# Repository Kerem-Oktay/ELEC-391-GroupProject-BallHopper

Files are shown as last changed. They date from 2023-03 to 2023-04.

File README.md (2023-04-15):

# Ball Hopper: Gripper Robot
ELEC 391 - Electrical Engineering Design Studio II (January - March 2023)

### Team Members
- Analog Electronics: [Idil Bil](https://github.com/idil-bil)
- Digital Electronics: [Kerem Oktay](https://github.com/Kerem-Oktay)
- Optimal Control: [Phi Lam](https://github.com/philam2001)
- System Identification: [Jaydon Alexis](https://github.com/jaydonalexis)

## Proof of Concept Videos
### Analog 
- Homing Circuit: https://drive.google.com/file/d/1XPwnbltA7bYrDxhqjHbavb2MQuFamWF6/view?usp=sharing
- Motor Driver Response to PWM Signals: https://drive.google.com/file/d/1h0WLaYGfkV7tp02XX7nt_eYF0rJrJksn/view?usp=sharing

### Digital
- Missed Pulses Test: https://drive.google.com/file/d/1QNyGvOfNERpase1NgM-POGZV6O9L-rX4/view?usp=sharing
- Both Directions Counting: https://drive.google.com/file/d/1wTb4RRv8bWMMX-Ec8G-Ff5oxxHRGX3V3/view?usp=sharing

### Optimal Control
- Gripper Mechanism Control: https://drive.google.com/file/d/1wUlJKEUdJ5kxWtdi2DNFExJYAqgorsBL/view?usp=sharing
- Interrup Service Routine Running: https://drive.google.com/file/d/1-M_vfCSoojId2iBqmILGAV9uz4eYeyNS/view?usp=sharing

### System Identification
- Gripper Mechanism Simulation on MATLAB/Simulink: https://drive.google.com/drive/folders/1JD9nbEjx4Q1AWdH3Mn-C0eqIqGHE8A6V?usp=sharing

## Other Videos
- The control system working before integration, with sensors: https://drive.google.com/file/d/1pgXOPBrIMusSZi8hItNfwTtvf7tGX0xt/view?usp=sharing
- Motor moving the fingers: https://drive.google.com/file/d/19ZQQKfPF29rKkGoej6QkP3fz3SBA11u9/view?usp=sharing
- The finger picking up a tennis ball: https://drive.google.com/file/d/1Nz7Qj5wmDarD6SwZJ-01VuMlN-VZ1lDX/view?usp=sharing

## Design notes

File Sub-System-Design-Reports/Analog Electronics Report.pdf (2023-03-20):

1

### Ball Hopper – Analog Electronics

White Paper | Updated – March 19, 2023
Idil Bil, Group Portugal, ECE, University of BC, Vancouver, BC, Canada

Abstract
An electrical hardware system for an autonomous tennis ball gripping robot is designed. The system consists of a microcontroller (ESP32), various peripherals, proximity sensors and a motor driver. Peripherals are used to interface with the user, proximity sensors are used to detect the objects and the destination, while the motor driver is used to control the motor.

In this paper, Section 1 defines the Analog sub-system behavior and identifies the RCGs to achieve that. Section 2 explains the design process for the sub-system including Part Selection, Motor Driver Design and PCB Design using MATLAB and Altium CircuitMaker. Lastly, Section 3 talks about the tests executed to verify if the designs satisfy the RCGs.

Nomenclature
RCG Requirement, Constraint, Goal PCB Printer Circuit Board
cm centimeter
A ampere
V voltage
ms | millisecond
IC | Integrated Circuit
MCU Microcontroller
PJA Power Jack
I/O Input/output
PLD Programmable Logic Device DC Direct Current
OTS Off the Shelf

2

MHz Mega Hertz
CPU Central Processing Unit
UART Universal Asynchronous Receiver/Transmitter SPI Serial Peripheral Interface
CPR Counts per Rotation
DRC Design Rule Checker
PWM Pulse Width Modulation LED Light Emitting Diode

### 1. RCG Identification

This project is an autonomous gripper robot. To ensure autonomous functionalities an analog electronic subsystem is designed. The system must have certain peripherals, proximity sensors, a motor to detect and grasp objects. In addition, a microcontroller is needed to use the mentioned devices. For this functionality the following 5 RCGs for the related issues are identified as shown in Figure 1.

Issue | Requirement | Constraint | Goal
Motherboard PCB | Board must fit a 6x8 cm area | All the peripherals need to align with proper mechanical placement in the enclosure box | Minimize board size
Motor Driver PCB | Board must fit a 6x5 cm area | Traces for the motor must hold up to 5 A | Minimize board size
Motor Driver Power Consumption | Must not consume more than 0.3 A at 12 V under no-load conditions | Power consumption can’t be smaller than 0.15 A at 12 V | Minimize the power consumption
Motor Driver Response | Step response settle time must be smaller than 200 ms | A minimum of 15% duty cycle is needed for the PWM to generate the response | Minimize the settle time

3

Homing
Circuit

Must be suited
for mechanical
interaction
between the
circuit and
fingers

Can’t be too sensitive, so it doesn’t register false homing

Minimize the
response
time

Figure 1: Analog Electronic RCG’s

### 2. Sub-System Design

In this section, the design choices for the hardware are explained. As a start, the High-Level Hardware Design talks about the overall architecture. Then, Part Selection specifies the electronic components chosen and why. Motor Driver Design explains the chosen IC and the characterization process. After that, Motherboard and the Motor Driver PCB Design explains the respected PCB design processes.

### 2.1 High-Level Hardware Design

Figure 2 presents the high-level architecture of the hardware. The functionalities of the blocks are as follows.

Power
- PJA: Supplies 12 V to the electronics.
- Power Regulator: Converts the 12 V input from the power jack into regulated 5V for other devices.
I/O
- Debug Port: Used to interface with the microcontroller.
- Digital Phone Jack: Used to reset and communicate the state of the gripper. Sensors
- Ultrasonic Sensor: Measure the distance between the gripper and the floor to detect when to grab objects.
- Hall Sensor: Detects the destination marker for object collection.

4

Motor Driver - Homing Circuit: Used to identify the end points of the fingers to start the reset

procedure. - Motor: Is the DC motor chosen in the System Identification Report. - Control Circuit: Is the Motor Driver Circuit explained in Section 2.3. - Decoder: Counts the pulses coming from the build-in encoder of the motor. - PLD: Acts as a multiplexer to feed the count bits to the microcontroller.

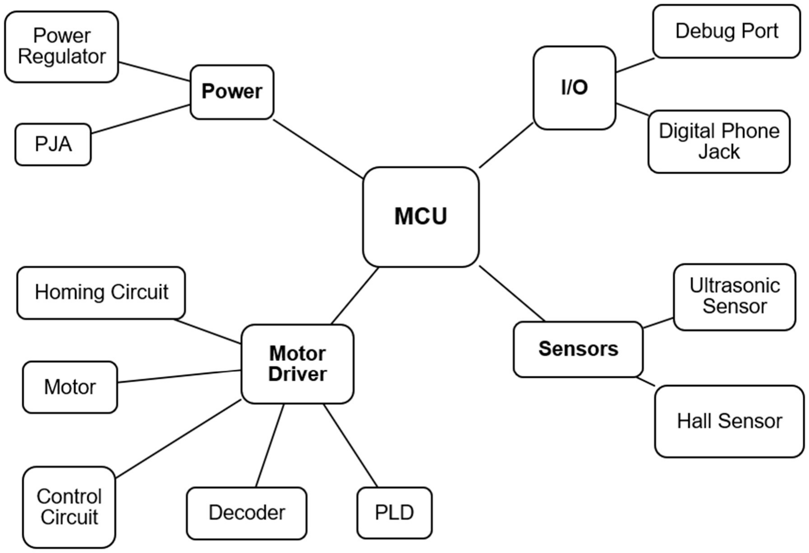
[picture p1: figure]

Figure 2: High Level Architecture Diagram

### 2.2 Part Selection

In order to achieve the functionalities mentioned above the following OTS products are selected and their connections are shown in the schematic prepared with Altium CircuitMaker in Figure 3:

5

ESP32-DOIT-DEVKIT V1 [1] is chosen as the microcontroller as it has the chip ESP32-D0WDQ6 [2], which provides 4 timers, 19 general purpose I/O and a prebuild debug port. It has a clock frequency between 80 MHz and 240 MHz, this is believed to be enough for our software in our current stage. It also provides dual CPU cores, that can be used for running multiple software simultaneously and supports a high variety of interfaces such as UART, SPI and Ethernet, which can be used for integration.

PJA is a user defined interface, so the device PJ-102A [3] given to us was used. For voltage regulation LM7805CT [4] is used as it provides regulated 5 V given a 12 V input.

Digital Phone Jack is also a user defined interface, so the device SJ1-3544N [5] given to us was used. Debug port is present in the chosen microcontroller.

The Ultrasonic Sensor is chosen as HC-SR04 [6] as it is a widely used and accurate ultrasonic sensor in the market. For the Hall Sensor the SS411P [7] is chosen because it has a build-in pull up resistor making the integration with the microcontroller simpler.

SS-01GLP [8] limit switch is used for the homing circuit as it provides mechanical interface that can be triggers using the fingers of the claw. The motor chosen is from Pololu with the item number 2821 [9]. This motor coming with a build-in encoder, has 64 CPR and needs a 12 V input, which fits our power circuit. Further explanation is in the System Identification Report. The decoder HCTL-2022 [10] is chosen because of reasons explained in the Digital Electronics Report. The Atmel ATF16V88 [11] PLDs are used as 4-1 multiplexers, which is also explained in the Digital Electronics Report. Lastly, the Control Circuit is a Motor Driver IC explained in Section 2.3.

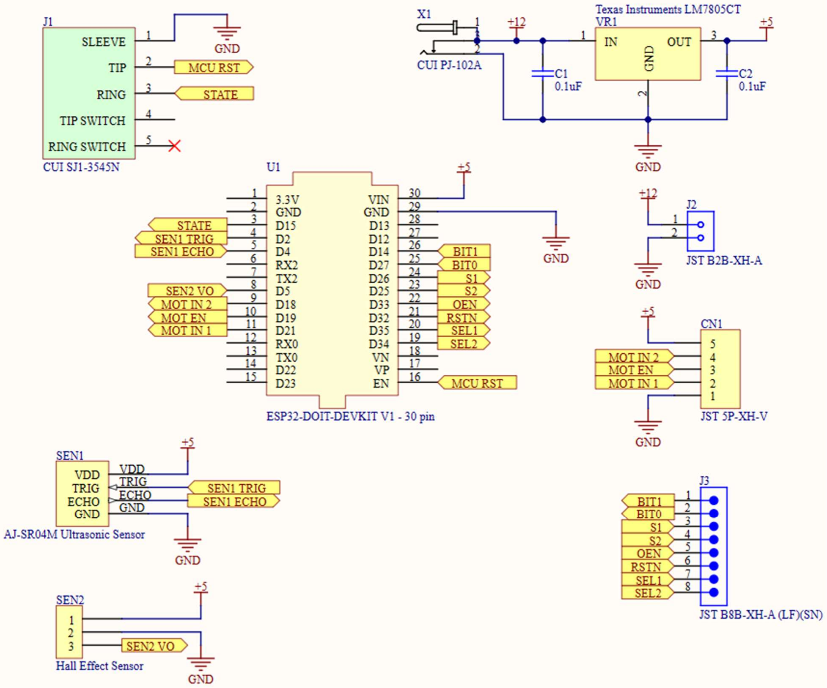
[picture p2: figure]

6

Figure 3: Motherboard Schematics

### 2.3 Motor Driver Circuit Design

The chosen motor driver being used is L298 Dual Full-Bridge Driver [12]. It’s block diagram obtained from the datasheet is shown on Figure 4. On the diagram, pin VS and VSS are respectively supply voltage and logic supply voltage. Pin numbered 8 is ground, pins labelled In1 and In2 are input signals for one H-bridge. Pin labelled EnA is the enable pin for the H-bridge of one motor. Out1 and Out2 are the output pins of that H-bridge and they connect to the motor chosen. Rest of the pins are not used as they are for a second motor which is not used in this project.

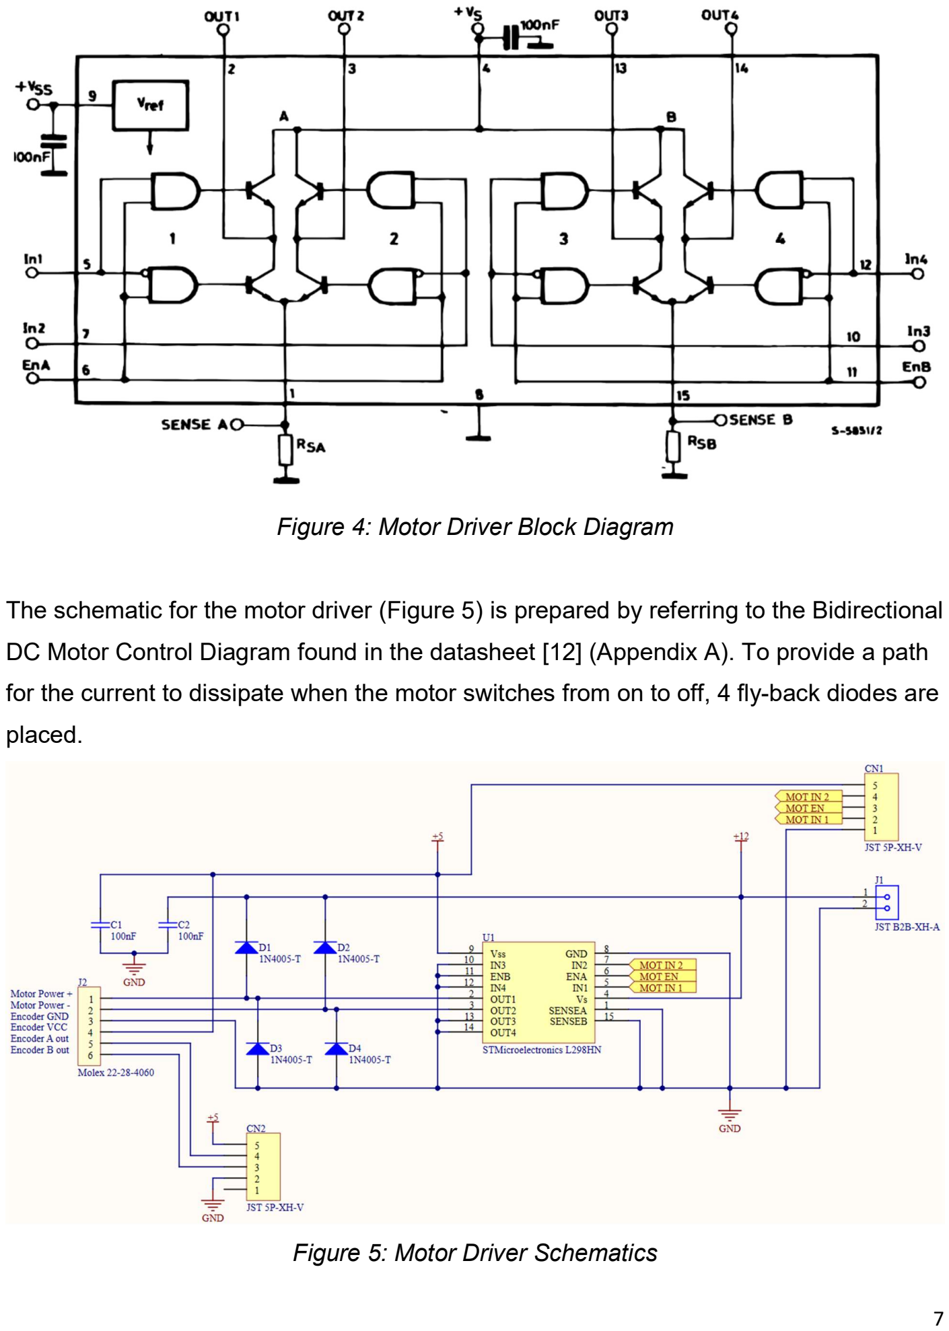
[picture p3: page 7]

7

Figure 4: Motor Driver Block Diagram

The schematic for the motor driver (Figure 5) is prepared by referring to the Bidirectional DC Motor Control Diagram found in the datasheet [12] (Appendix A). To provide a path for the current to dissipate when the motor switches from on to off, 4 fly-back diodes are placed.

Figure 5: Motor Driver Schematics

8

The characterization of the motor is done by collecting data from the oscilloscope to be used by Optimal Control. 5 V was given to In1 and In2 of the motor driver to get the step response seen in Figure 6.

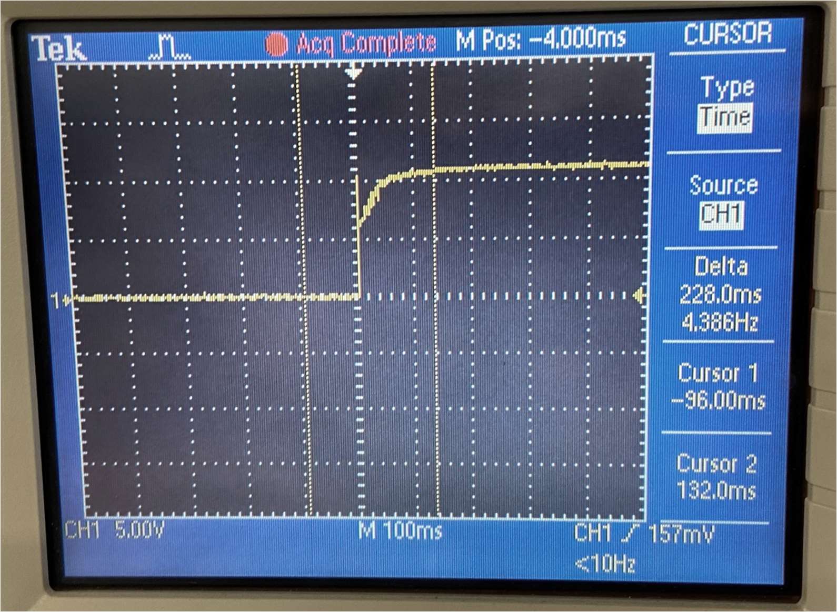
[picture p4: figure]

Figure 6: Step Response of the Motor Driver

This data acquisition is done multiple times to calculate the approximate settle time as 130 ms and the MATLAB code found in Appendix B is used to calculate the transfer function in Figure 7 and the step response in Figure 8. The settle time was lower than 200 ms and it was only consuming around 0.21 A at 12 V. Since these satisfies the RCGs and the step responses looked similar this driver was chosen.

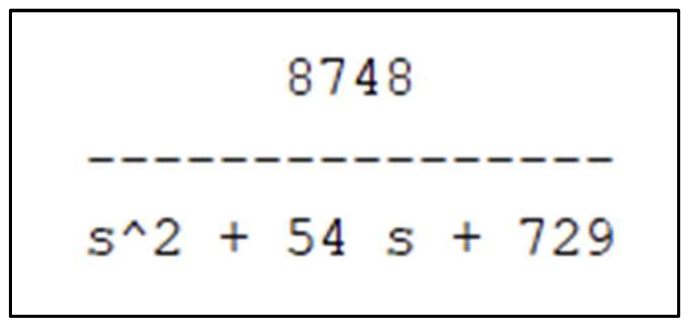
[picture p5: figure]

Figure 7: Motor Driver Transfer Function

9

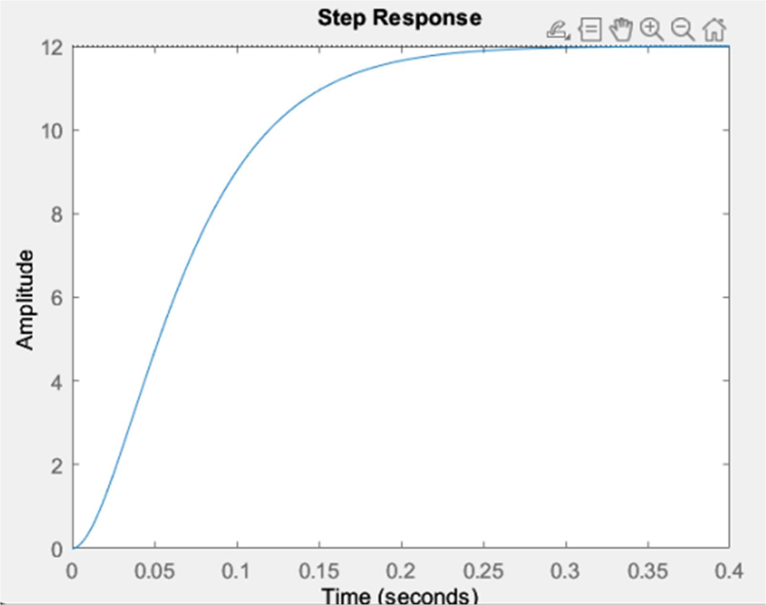
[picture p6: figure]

Figure 8: Motor Driver Step Response

### 2.4 Motherboard and Motor Driver PCB Design

Using Altium CircuitMaker, a Motherboard for the Microcontroller and the peripherals, as well as, a Daughterboard for the Motor Driver Circuit are designed. The boards are 2-layered with no ground plane. Each board has dedicated XH-connecters for board-toboard connections. All the components are properly named, and their labels can be seen on the silkscreens. Figure 9 and 11 show the PCB schematics, while Figure 10 and 12 show the 3D view of the PCBs.

To meet the size RCG, the PLDs and the decoder were put on a different Daughterboard that is explained in the Digital Electronics Report.

10

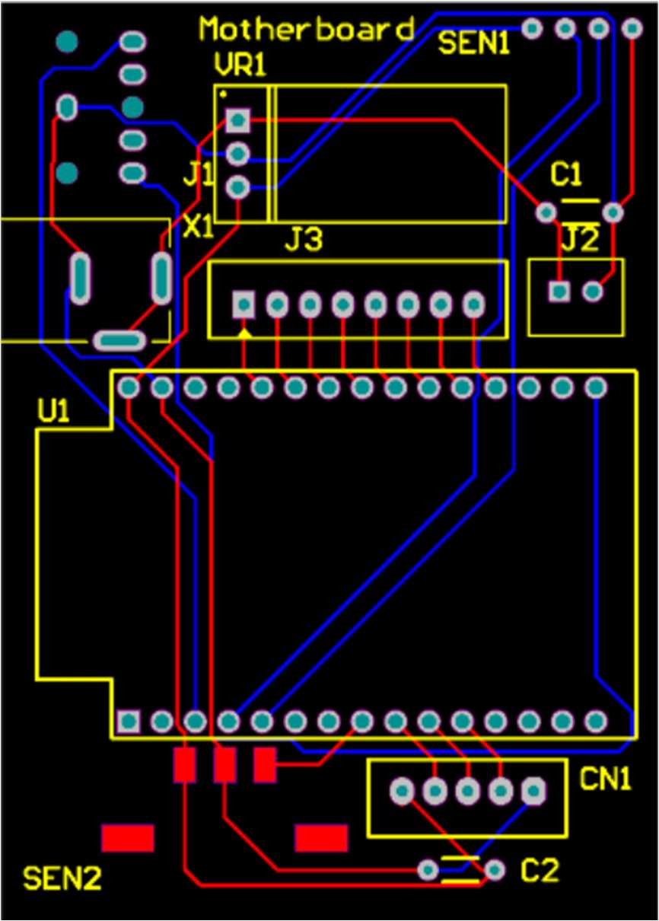
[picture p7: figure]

Figure 9: 2D View of the Motherboard PCB

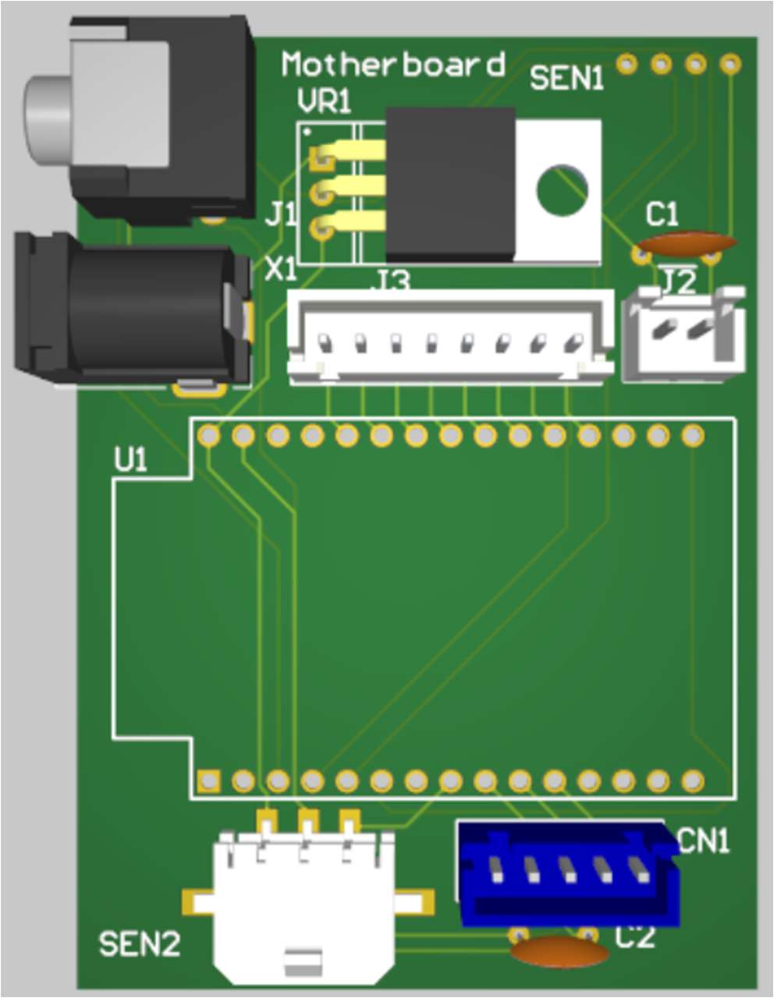
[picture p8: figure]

Figure 10: 3D View of the Motherboard PCB

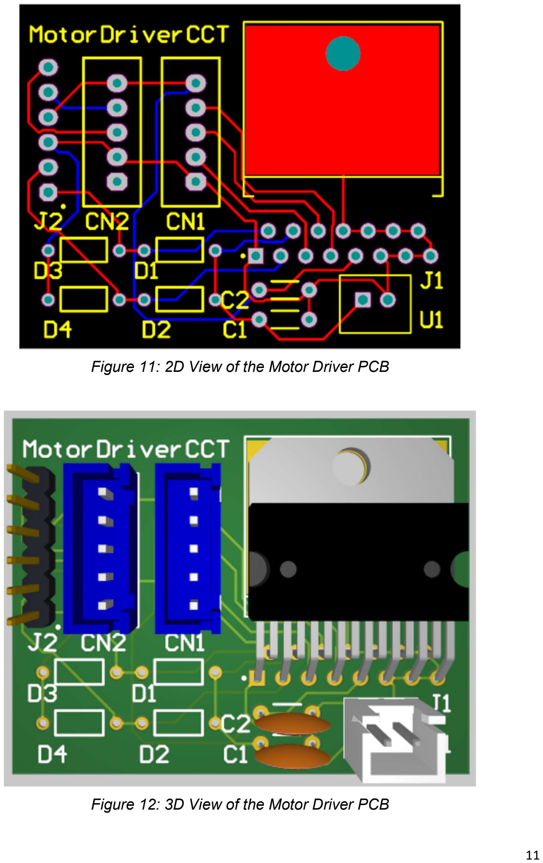
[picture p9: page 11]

11

Figure 11: 2D View of the Motor Driver PCB

Figure 12: 3D View of the Motor Driver PCB

12

### 3. Testing of the Design

The 5 RCGs listed in Section 1 are either individually tested or considered in the design process. The tests executed, and their results are explained below.

### 3.1 Motherboard PCB

The “Run DRC” feature in Altium CircuitMaker is used to verify the PCB design made, refer to Appendix C for the “DRC Report”. The size requirement was kept in mind while designing the board for the first iteration. Iterations following that focused on minimizing the board size. Current board size is 5x7 cm, the RCG has been met.

### 3.2 Motor Driver PCB

Same approach as the Motherboard is used when designing the PCB for the Motor Driver. The “Run DRC” feature in Altium CircuitMaker is used to verify the PCB design made, refer to Appendix D for the “DRC Report”. First iteration was made while keeping the size requirement in mind and the following iterations minimized the board size. Current board size is 4.5x3.5 cm, the RCG has been met.

### 3.3 Motor Driver Power Consumption

Multiple tests where the Motor Driver was connected to a 5 V input were run. Figure 13 shows the power supply photo where the current was as low as 0.18 A. However, on average the power consumption under a no-load case was found to be 0.21 A at 12 V. These numbers meet the RCGs identified.

13

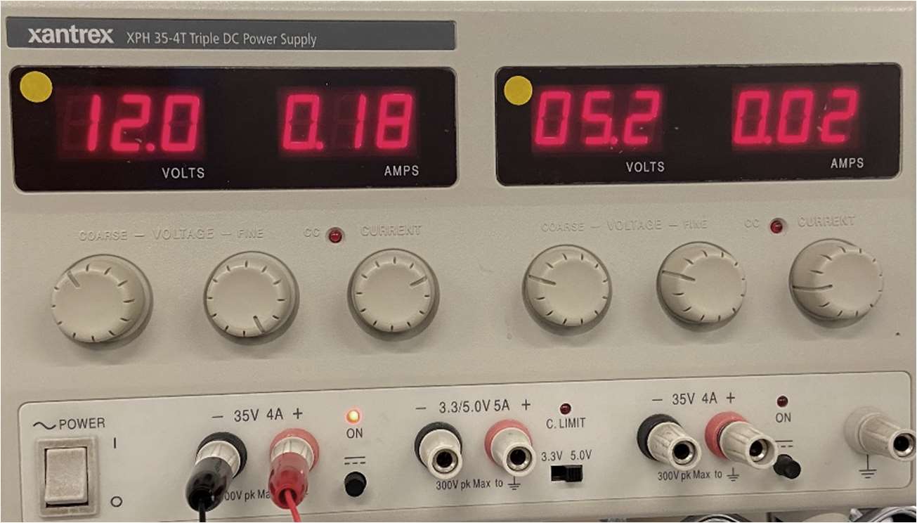
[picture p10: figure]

Figure 13: Power Supply Data for the Motor Driver

### 3.4 Motor Driver Response

As seen in Section 2.3 the Motor Driver has a settle time of 130 ms. Other tests were run with a custom build H-bridge, which also consumed 0.2 A at 12 V under no-load conditions. However, it had a settle time of 180 ms, so due to the lower settle time of the IC, L298 was chosen as the Motor Driver. Refer to Appendix E for the step response of the H-bridge.

The video “Motor-Driver-Response-to-PWM Signals” (https://drive.google.com/file/d/1h0WLaYGfkV7tp02XX7nt_eYF0rJrJksn/view?usp=shari ng) shows the Motor Driver operating under different PWM duty cycles. When the duty cycle is doubled the speed also approximately doubled. This data can be seen on the proof of concept video.

### 3.5 Homing Circuit

A straightforward test circuit was prepared for the limit switch. By clicking the switch, the circuit was complete, and the LED was lit. Since this mechanical interface can be used with the fingers of the gripper, this component can be used as the Homing Circuit and

14

the RCG is met. Refer to the video “Homing-Circuit” (https://drive.google.com/file/d/1XPwnbltA7bYrDxhqjHbavb2MQuFamWF6/view?usp=sh aring) to see the test being run.

References
[1] “ESP32-DevKitC V4 Getting Started Guide - ESP32 - — ESP-IDF Programming Guide latest documentation,” Espressif.com, 2016. [Online]. Retrieved March 19, 2023, from https://docs.espressif.com/projects/esp-idf/en/latest/esp32/hw-reference/esp32/get-starteddevkitc.html.
[2] ESP32 Series Datasheet Including. (n.d.). Retrieved March 19, 2023, from https://www.mouser.ca/datasheet/2/891/Espressif_Systems_01292021_esp32-1991551.pdf
[3] "PJ-102A Datasheet - Jacks | Dc Power Connectors | CUI Devices," Retrieved March 19,
2023, from https://www.mouser.ca/datasheet/2/670/pj_102a-1778834.pdf
[4] "LM78XX, LM78XXA - 3-Terminal 1 A Positive Voltage Regulator," . Retrieved March 19, 2023, from https://www.mouser.ca/datasheet/2/308/LM7805-1301244.pdf
[5] "SJ1-354XN Series Datasheet - Jacks | Audio Connectors | CUI Devices," . Retrieved March
19, 2023, from https://www.mouser.ca/datasheet/2/670/sj1_354xn_series-1779189.pdf
[6] "HC-SR04," . Retrieved March 19, 2023, from https://www.electroschematics.com/wpcontent/uploads/2013/07/HCSR04-datasheet-version-1.pdf
[7] "SS311PT/SS411P Bipolar Hall-Effect Digital Position Sensor ICs with Built-in Pull-up Resistor," . Retrieved March 19, 2023, from https://prodedam.honeywell.com/content/dam/honeywell-edam/sps/siot/en-us/products/sensors/magneticsensors/bipolar-position-sensor-ics/common/documents/sps-siot-ss311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
[8] “SS-P," . Retrieved March 19, 2023, from https://omronfs.omron.com/en_US/ecb/products/pdf/en-ss_p.pdf

15

[9] "MOT2-info.pdf," . Retrieved March 19, 2023, from https://people.ece.ubc.ca/~engservices/files/courses/elec391-data_sheets/MOT2-info.pdf
[10] "HCTL-2032,2022.pdf," . Retrieved March 19, 2023, from https://media.digikey.com/pdf/Data%20Sheets/Avago%20PDFs/HCTL-2032,2022.pdf
[11] "ATMEL ATF16V8B" . Retrieved March 19, 2023, from http://ww1.microchip.com/downloads/en/devicedoc/atmel-0364-pld-atf16v8b-8bq-8bqldatasheet.pdf
[12] "Dual full-bridge driver," . Retrieved March 19, 2023, from https://www.sparkfun.com/datasheets/Robotics/L298_H_Bridge.pdf

Appendix
A: Bidirectional DC Motor Control Block Diagram

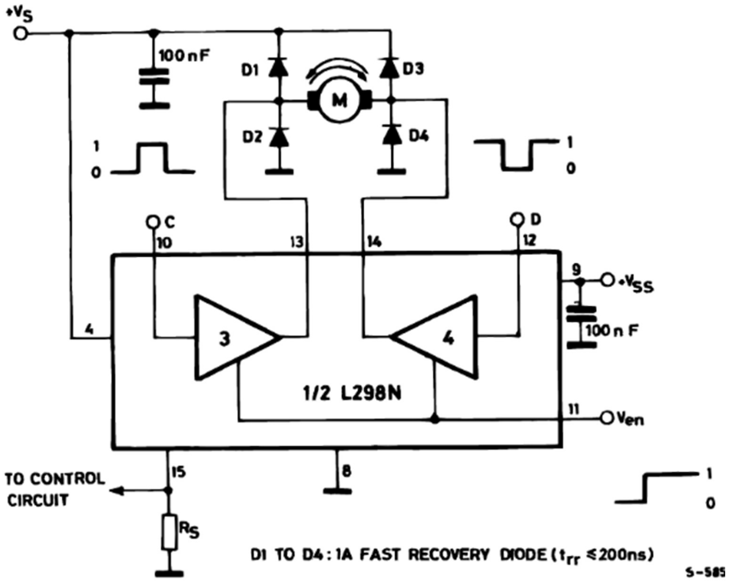
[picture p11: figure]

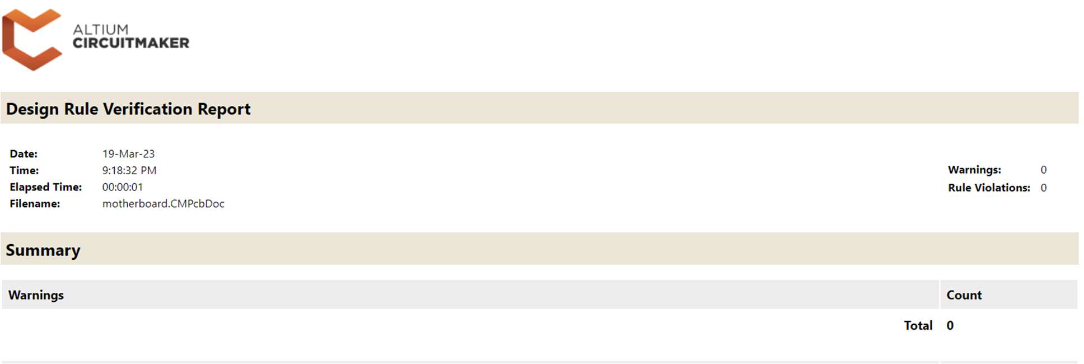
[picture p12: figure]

16

B: MATLAB Code for the Transfer Function

function naturalFrequency = getSettleTimeNaturalFrequency(settleTime, dampingCoefficient, timeConstantMultiplier)

naturalFrequency = fraction(timeConstantMultiplier, (dampingCoefficient * settleTime));

end

timeConstantMultiplier = 5

dampingCoefficient = 1

function transferFunction = getTransferFunction(naturalFrequency, gain, dampingCoefficient)

transferFunction = minreal(tf((((naturalFrequency)^2) * gain), [1 (2 * dampingCoefficient * naturalFrequency) ((naturalFrequency)^2)]));

end

C: DRC Report for the Motherboard

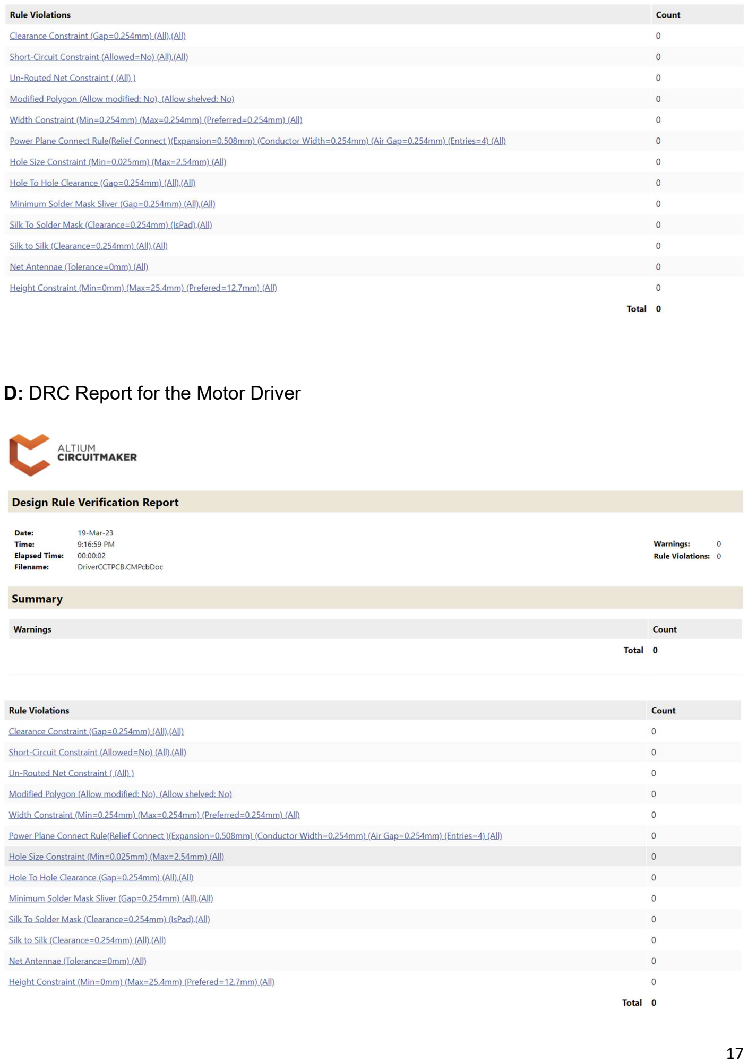
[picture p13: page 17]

17

D: DRC Report for the Motor Driver

18

E: Step Response of the Custom Build H-Bridge

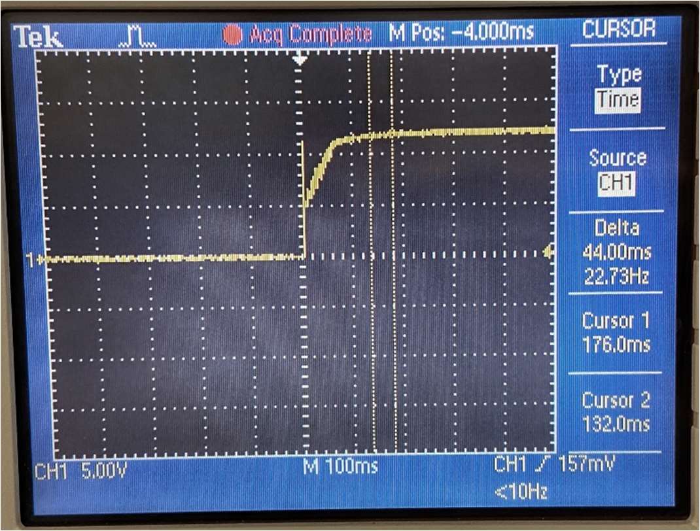
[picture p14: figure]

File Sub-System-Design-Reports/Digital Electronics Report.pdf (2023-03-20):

1

Ball Hopper – Digital Electronics

White Paper | Updated – March 19, 2023
Kerem Oktay, Group Portugal, ECE, University of BC, Vancouver, BC, Canada

Abstract
A pulse counter-decoder system counting the encoder A and B signals coming from a built-in encoder of a motor is designed. The system consists of a quadrature decoder, HCTL-2022, and two PLDs, Atmel ATF16V8B, that are programmed as 4 to 1 multiplexers. Decoder reads the raw encoder signals coming from the motor and converts them to a single 32-bit count value. Multiplexers are used to minimize wiring while keeping maximum bits for the count signal. C code is developed to read the signal and convert it to motor angle value for later usage.

In this paper, Section 1 defines the sub-system behavior and identifies the RCGs to achieve the behavior. Section 2 explains the Sub-System design by going through the parts of the system and the design process using tools such as WinCUPL/WinSim and Altium CircuitMaker. Finally, Section 3 goes over the tests executed to verify the designed system satisfies the RCGs. Nomenclature
RCG | Requirement, Constraint, Goal
IC | Integrated Circuit
MHz | Mega Hertz
CW/CCW Clockwise/Counter-Clockwise
MCU | Microcontroller Unit
CPR | Counts Per Revolution
PCB | Printed Circuit Board
DRC | Design Rule Check
MUX | Multiplexer
PLD | Programmable Logic Device
PWM | Pulse Width Modulation
POC-VID Proof of Concept Video

2

### 1. RCG Identification

In this project a DC motor with a built-in encoder is used. A digital electronics sub-system is designed to ensure proper reading and converting of the pulses coming from the encoder. The system must read the encoder A and B signals, count the pulses while keeping track of the direction and convert the count value into motor angle. From this defined functionality of the system, the following 5 RCGs for related issues are identified as shown in Table 1.
Issue | Requirement | Constraint | Goal
Pulse Counting | The system must not miss more than 10 pulses per 100 pulses. | The clock frequency of the decoder IC cannot exceed 33MHz. | Minimize the number of missed pulses.
Motor Direction Detection | The system must realize when the motor is rotating in CW and CCW directions. | Negative directions must be registered as 2’s complement values. | Minimize the usage of different logic for the direction detection.
Wiring/Bit Usage | Pulses must be counted with at least 10 bits to avoid quick overflows. | Atmel ATF16V8Bs (PLDS) have a set number of Input and Output pins. | Maximize the bits for counting and minimize external wiring of the MCU.
Pulse Conversion into Degrees | Angle value resolution must be at least the same as the resolution CPR of the encoder. | The encoder has a set value of 64 CPR. | Maximize the resolution of the degree values.
Daughter Board | The PCB must be smaller than 6x6 cm. | The PCB cannot violate any DRC points. | Minimize the size of the PCB.

Table 1: Digital Electronics Sub-System RCGs

3

### 2. Sub-System Design

This sub-system consists of HCTL-2022, a Quadrature Decoder / Counter Interface IC, and 2 PLDs. This section first goes over the characteristics of the quadrature decoder IC. Afterwards, it explains the high level and 4-1 MUX design. Finally, it presents the integration of HCTL-2022 and 4-1 MUXs, the PCB design and the C code developed for degree value conversion.

### 2.1. HCTL-2022 Characteristics

HCTL-2022 counts the pulses of an encoder given the A and B signals as input. It counts with 32 bits and can run up to 33 MHz clock frequency. It has tri-state buffers to output a single byte (8 bits) of the count value. The pinout of the IC is shown at Figure 1. This diagram is obtained from the datasheet of the IC [1]. Pins D0-D7 are the 8 bits of a selected byte. Pins SEL1 and SEL2 are selection signals for outputting certain bytes of the count value. OE pin is used to enable/disable the tri-state buffers and RST pin is used to reset the IC. CHA and CHB are the input signals fed from the encoder of the motor. Other pins are not used in this design.

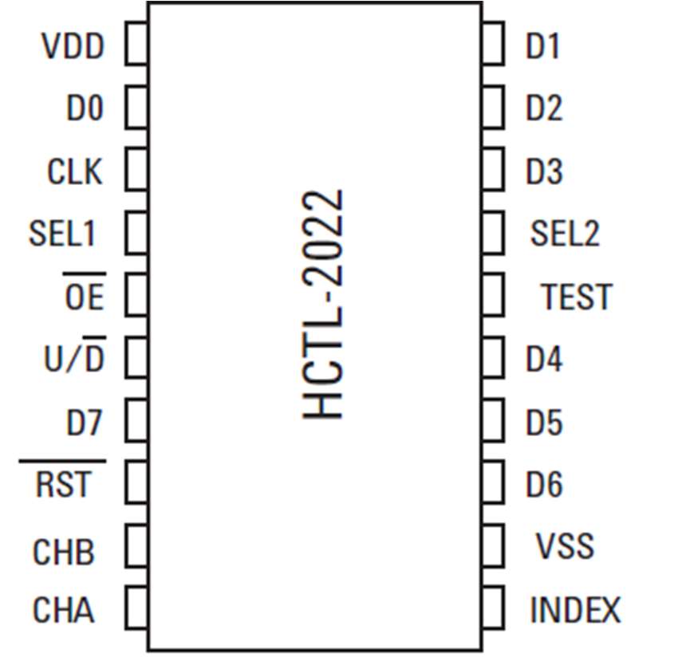
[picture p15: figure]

Figure 1: Pinout of HCTL-2022 Due to the digital noise filtering, high clock frequency, 32 bits up and down counting and latch capabilities; HCTL-2022 is chosen in this design. These features address the Pulse Counting, Motor Direction Detection and Wiring/Bit Usage RCGs.

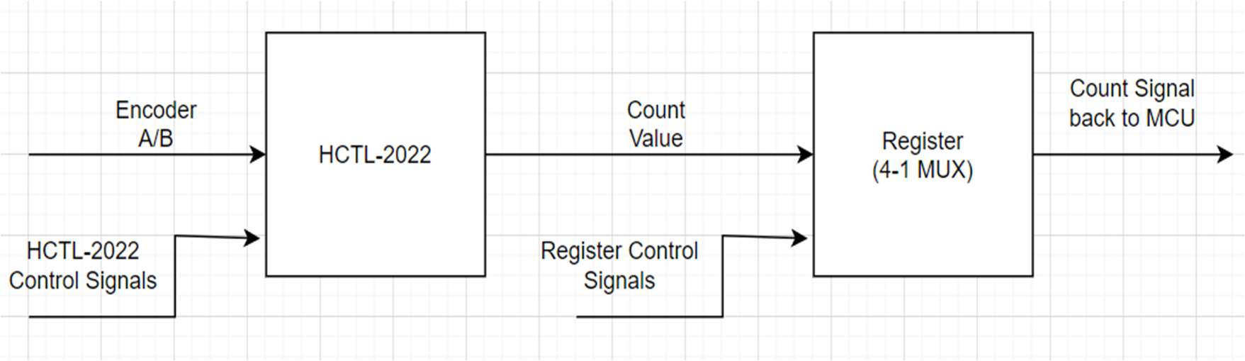
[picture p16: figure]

4

### 2.2. High Level Decoder Design

The high-level decoder system design is shown at Figure 2. The system is provided encoder A and B signals, and control signals for HCTL-2022 and register block. The chosen register block is a 4-1 MUX. The count value is fed back to an MCU.

Figure 2: High-Level Decoder System Design Since HCTL-2022 needs 8 bits for its output and 4 bits for its control, using it alone requires 12 bits that needs to be externally wired to MCU board. By using two 4-1 MUXs, there are only 2 bits for output and 2 bits for MUX control in addition to the 4 bits for HCTL-2022 control. This adds to 8 bits which satisfies the goal of “Wiring/Bit Usage” RCG. This way a single byte is read in 4 pairs of bits.

2.3. 4-1 MUX Design
Atmel ATF16V8B model PLDs are used to design the 4-1 MUXs. The truth table for a 4-1 MUX is shown at Table 2. S1 and S2 are selection signals. Q0 is the output of the MUX and D0-D3 are the input signals.
S1 | S2 | Q0
0 | 0 | D0
1 | 0 | D1
0 | 1 | D2
1 | 1 | D3
Table 2: 4-1 MUX Truth Table

5

By observing the truth table, the following circuit schematics in Figure 3 is built using logic gates. S1 and S2 are the same signals as on the Truth Table, I0-I3 correspond to D0-D3 and Y corresponds to Q0.

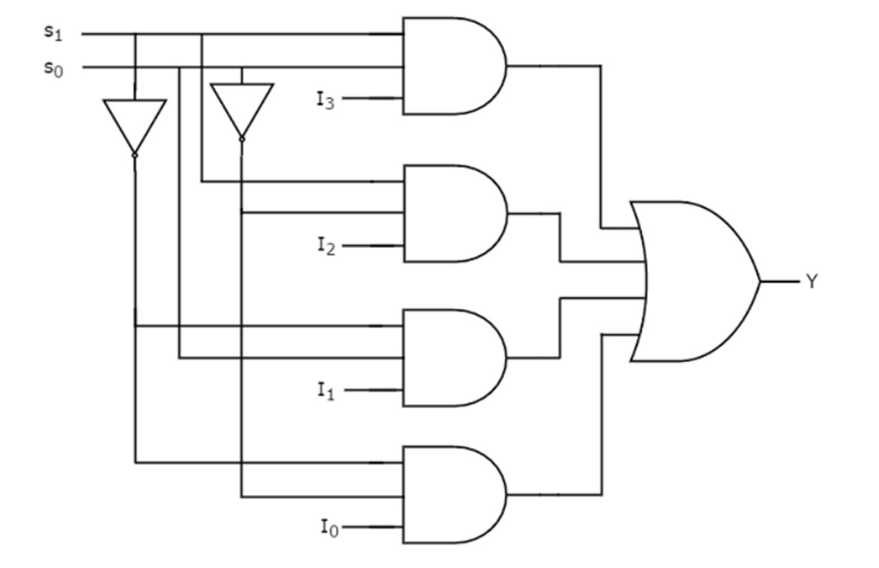
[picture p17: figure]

Figure 3: 4-1 MUX Circuit Schematic with Logic Gates [2] The logic equation written in CUPL language in WinCUPL is as follows (1). The variables are the same signals as shown on the Truth Table.

Q0 = (D0 & !S1 & !S2) # (D1 & S1 & !S2) # (D2 & !S1 & S2) # (D3 & S1 & S2); (1)

The design is simulated using WinSim and the following waveform is obtained shown at Figure 4. The waveform matches with the desired Truth Table.

6

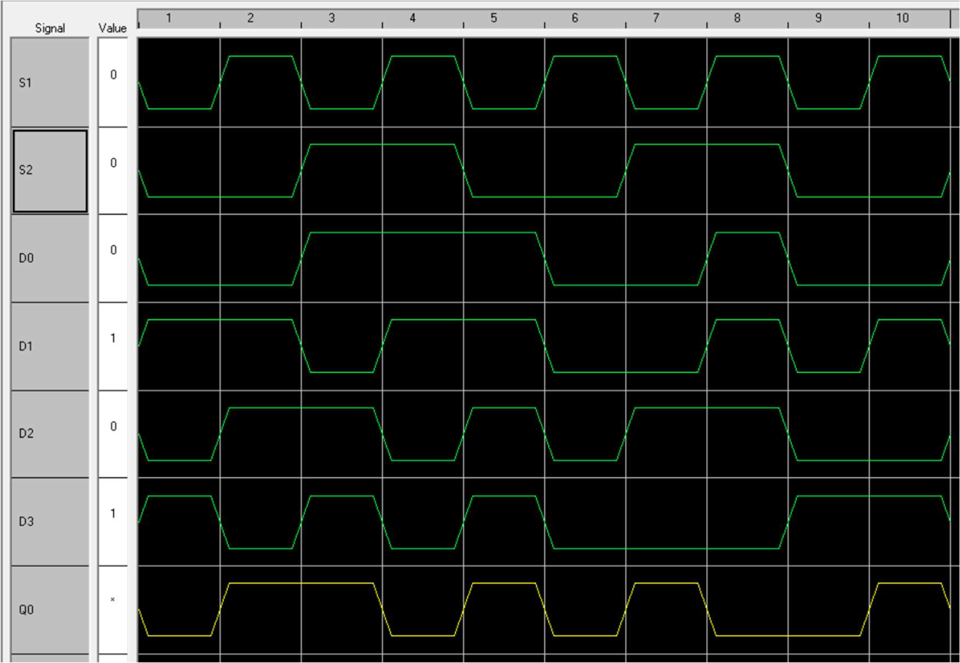
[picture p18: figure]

Figure 4: 4-1 MUX Simulated Waveform

### 2.4. HCTL-2022 IC and 4-1 MUX Integration

HCTL-2022 and 4-1 MUXs (PLDs) are integrated by simply connecting the D0-D3 outputs of the HCTL-2022 to inputs of one of the MUXs and D4-D7 outputs to the inputs of the other MUX. All control signals are fed from an MCU and output signals BIT0 and BIT1 are fed back to the MCU. The schematic prepared with Altium CircuitMaker is shown in Figure 5. Connectors are added for wiring between the motherboard and a crystal is added to provide clock for HCTL-2022.

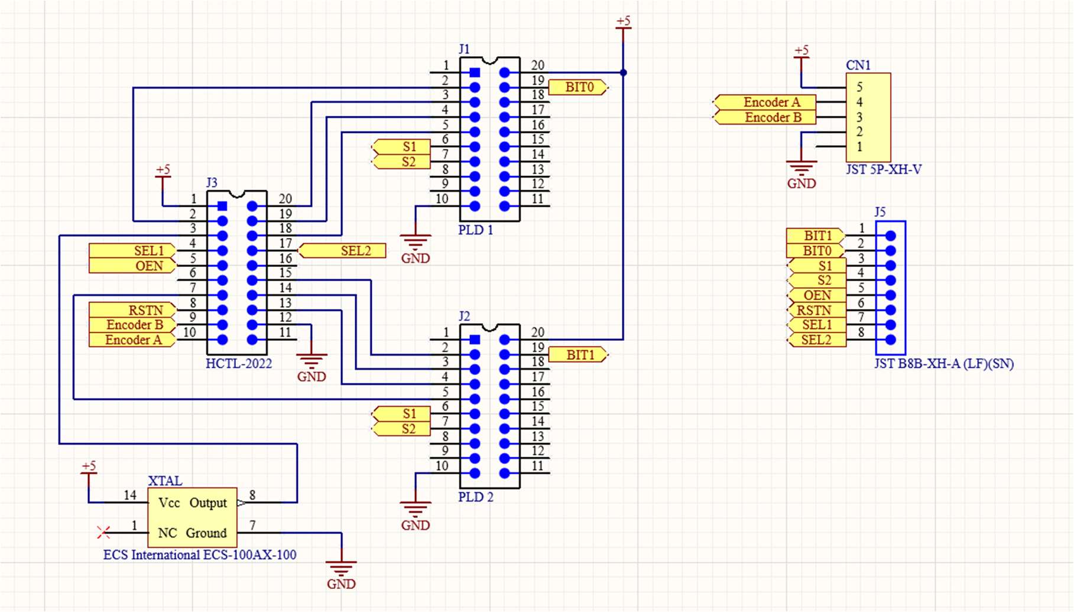
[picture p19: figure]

7

Figure 5: Decoder System Circuit Schematic

### 2.5. Daughter Board PCB Design

Using Altium CircuitMaker a daughter board called Pulse Counter is designed. The board consists of two-layers with no ground-plane. As the HCTL-2022 and ATF16V8B devices are through hole devices, 20-pin DIP sockets are put in their places. XH type connectors are used to connect the daughter board to motor driver board and motherboard. Figures 6 and 7 show the PCB schematics and 3D view of the Pulse Counter PCB.

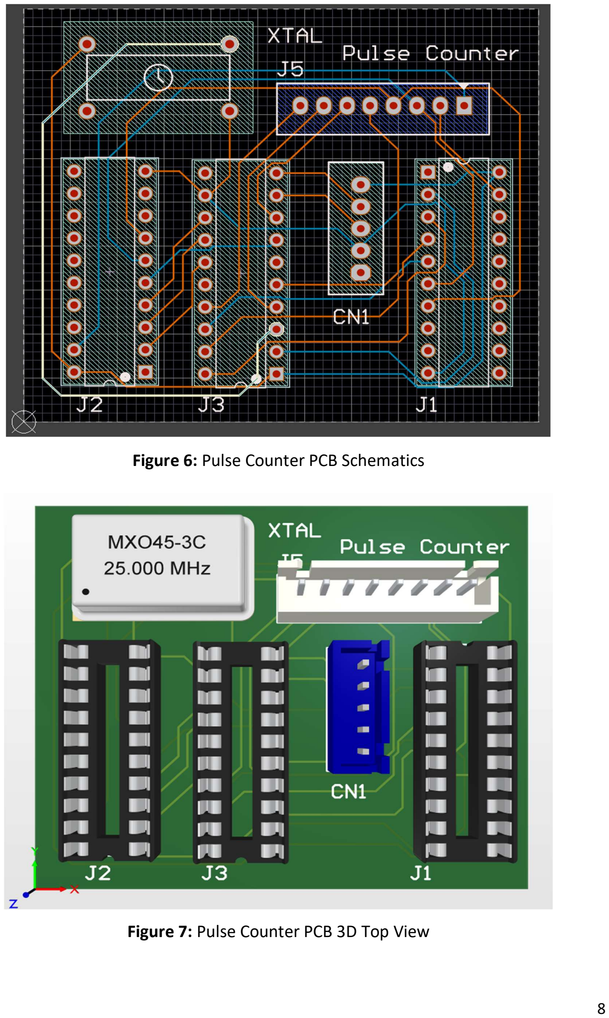
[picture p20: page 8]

8

Figure 6: Pulse Counter PCB Schematics

Figure 7: Pulse Counter PCB 3D Top View

9

### 2.6. C Code Design for Degree Conversion

As the signals coming from the decoder system are raw bits that carry the pulse count, a software routine is necessary to convert this value into degrees of the motor. In this report the C code logic is explained through an Arduino UNO board that is used for testing the system.

The routine is shown on the Flow Diagram on Figure 8. By setting SEL1 and SEL2 to corresponding HIGH and LOW values as described in page 6 of the HCTL-2022 datasheet and disabling the OE signal, certain bytes are registered [1]. Then by setting S1 and S2 signals for the 4-1 MUXs, bytes are read in 4 pairs of bits.

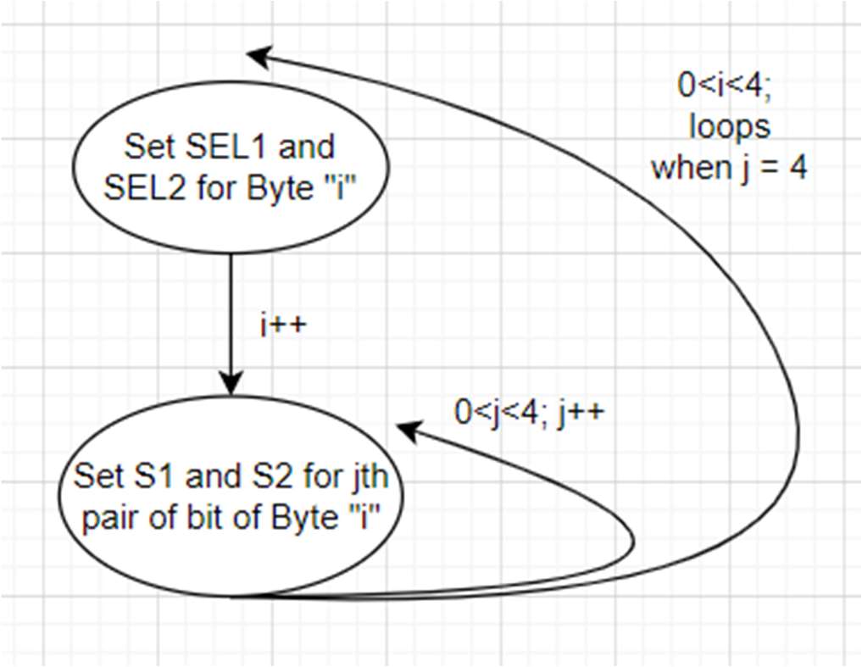
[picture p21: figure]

Figure 8: Software Routine Flow Diagram After getting all 4 bytes, these bytes are combined into a single 32 bit variable. This byte is the count value. As there is 64 CPR, it means every 360 degrees the decoder has counted 64 pulses. Therefore by multiplying the count value by 360/64, the angle value of the motor is obtained.
Please refer to the Appendix A for the full C code developed.

### 3. Testing of the Design

The 5 RCGs listed in the first section are individually tested or considered during the design process. The tests executed and their results are explained below.

10

i) Pulse Counting

After resetting the quadrature decoder and motor position, the motor driver is fed with constant 5V input. This case is assumed as the highest speed as there is no load present to slow the motor down and in terms of a PWM signal this corresponds to 100% duty cycle.

The motor is run for a certain amount of time and then stopped. The position of the motor is brought to the initial position by aligning the marker lines. The angle value (a value between 0 and 360 degrees that resets after every rotation) is seen to be 0 degrees again. This indicates no pulses were missed as any missed pulse would create an offset between the initial position and angle value of 0 degrees.

This test shows that the RCG is met. Please refer to POC-VID1 for the test being run.

ii) Motor Direction Detection

HCTL-2022 counts the pulses in both directions by increasing or decreasing the same count value. By using variable types in the C code that detect 2’s complement, negative values are detectable as well. The code does not take separate actions for two cases which means the logic is minimalized.

This shows that the RCG is met. Please refer to POC-VID2 for the test being run.

iii) Wiring/Bit Usage

HCTL-2022 counts with 32 bits which is above the 10 bits requirement. Two 4-1 MUXs in PLDs also minimize the external wire usage while keeping the same number of 32 bits counting. HCTL-2022 requires 4 wires. Using the MUXs only adds 4 more wires making a total of 8 wires.

This shows that the RCG is met during the design process.

11

iv) Pulse Conversion into Degrees

As every pulse count is registered properly by the MCU, the resolution is the same as resolution of the built-in encoder. Due to this value being set, it is also the maximum achievable resolution.

This shows that the RCG is met. Please refer to either POC-VID1 or POC-VID2 to see the angle values being reported through the serial port.

v) Daughter Board

After completing the PCB layout, “Run DRC” feature is used to verify the PCB design. While designing the board, the board size is first set to the Requirement value. After completing the design small changes are made to decrease the size of the board. The current final board is 5.5cmx4.7cm.

This shows that the RCG is met during the design process. Please refer to the Appendix B for the generated DRC document by the Altium CircuitMaker.

References

[1] "HCTL-2032,2022.pdf," . Retrieved March 19, 2023, from https://media.digikey.com/pdf/Data%20Sheets/Avago%20PDFs/HCTL-2032,2022.pdf
[2] "Digital Circuits - Multiplexers," . Retrieved March 19, 2023, from https://www.tutorialspoint.com/digital_circuits/digital_circuits_multiplexers.htm

12

Appendix A. C Code for Angle Value Conversion

// Control Signals
int RSTN = 2;
int OEN = 3;
int SEL1 = 4;
int SEL2 = 5;
int S1 = 6;
int S2 = 7;

// Counter Signals
int BIT0 = 8;
int BIT1 = 9;

volatile long count = 0;

/*
The algorithm below is based on the Example Routine given in the IC datasheet */

void setup()
{
// Assign Output Pins
pinMode(RSTN,OUTPUT);
pinMode(OEN,OUTPUT);
pinMode(SEL1,OUTPUT);
pinMode(SEL2,OUTPUT);
pinMode(S1,OUTPUT);
pinMode(S2,OUTPUT);

// Assign Input Pins

13

pinMode(BIT0,INPUT);
pinMode(BIT1,INPUT);

// Initial Decoder Reset
digitalWrite(RSTN,LOW);
delay(15);
digitalWrite(RSTN,HIGH);

// Initial Control Signals digitalWrite(OEN,LOW);
digitalWrite(SEL1,LOW);
digitalWrite(SEL2,LOW);
digitalWrite(S1,LOW);
digitalWrite(S2,LOW);

// Serial Port for Debug Purposes Serial.begin(9600);
}

byte getByte()
{
byte capture1 = 0; // Initialize a byte variable to read the first capture for(int i=0; i<4; i++){

switch(i){
case 0:
digitalWrite(S1,LOW);
digitalWrite(S2,LOW);
break;
case 1:

14

digitalWrite(S1,HIGH);
digitalWrite(S2,LOW);
break;
case 2:
digitalWrite(S1,LOW);
digitalWrite(S2,HIGH);
break;
case 3:
digitalWrite(S1,HIGH);
digitalWrite(S2,HIGH);
break;
default:
digitalWrite(S1,LOW);
digitalWrite(S2,LOW);
break;
}

capture1 |= (digitalRead(BIT0)<<i); capture1 |= (digitalRead(BIT1)<<(i+4));
}

byte capture2 = 0; // Initialize a byte variable to read the second capture for(int i=0; i<4; i++){

switch(i){
case 0:
digitalWrite(S1,LOW);
digitalWrite(S2,LOW);
break;
case 1:

15

digitalWrite(S1,HIGH);
digitalWrite(S2,LOW);
break;
case 2:
digitalWrite(S1,LOW);
digitalWrite(S2,HIGH);
break;
case 3:
digitalWrite(S1,HIGH);
digitalWrite(S2,HIGH);
break;
default:
digitalWrite(S1,LOW);
digitalWrite(S2,LOW);
break;
}

capture2 |= (digitalRead(BIT0)<<i); capture2 |= (digitalRead(BIT1)<<(i+4));
}

if (capture2 == capture1){ // If the first and second capture match then return the result byte byteCapture = capture2;
return byteCapture;
}
else getByte(); // If the first and second capture DO NOT match, try again to capture }

long combine4Bytes(byte byte4, byte byte3, byte byte2, byte byte1)
{

16

long combine = 0;
combine |= (((long)byte4 << 24) | ((long)byte3 << 16) | ((long)byte2 << 8) | ((long)byte1 << 0));
return combine;
}

void getPulseCount()
{
delay(25);
digitalWrite(OEN, HIGH); // Disable OE digitalWrite(OEN, LOW); // Enable OE

// SEL1 = 0 and SEL2 = 1 gets 4th Byte digitalWrite(SEL1, LOW);
digitalWrite(SEL2, HIGH);
byte Byte4 = getByte();

// SEL1 = 1 and SEL2 = 1 gets 3rd Byte digitalWrite(SEL1, HIGH);
digitalWrite(SEL2, HIGH);
byte Byte3 = getByte();

// SEL1 = 0 and SEL2 = 0 gets 2nd Byte digitalWrite(SEL1, LOW);
digitalWrite(SEL2, LOW);
byte Byte2 = getByte();

// SEL1 = 1 and SEL2 = 0 gets 1st Byte digitalWrite(SEL1, HIGH);
digitalWrite(SEL2, LOW);
byte Byte1 = getByte();

17

digitalWrite(OEN, HIGH); // disable OE
delay(25);
count = combine4Bytes(Byte4,Byte3,Byte2,Byte1); }

void loop() {
// put your main code here, to run repeatedly: delay(25);
digitalWrite(OEN, HIGH); // Disable OE

getPulseCount();

float angle = (count % 64)*(360.0/64.0) ; float angle_abs = (count)*(360.0/64.0) ;

Serial.print("Counter: "); Serial.println(count);

Serial.print("Angle: ");
Serial.println(angle);

Serial.print("Absolute Angle: "); Serial.println(angle_abs);

Serial.println("\n");
}

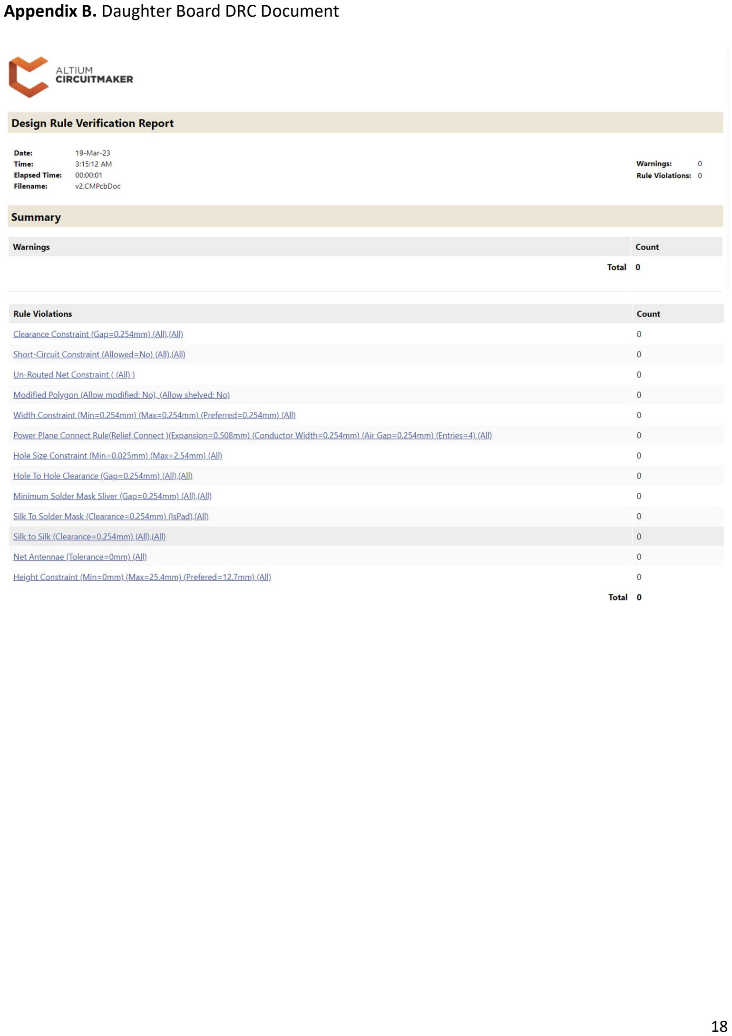
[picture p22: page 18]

18

Appendix B. Daughter Board DRC Document

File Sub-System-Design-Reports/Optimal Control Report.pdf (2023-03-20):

Ball Hopper – Optimal Control

White Paper | Updated – Mar 19, 2023
Phi Lam, Group Portugal, ECE, University of BC, Vancouver BC, Canada

Abstract
Our project is designed to be a tennis ball hopper and an important part of this robotic claw system is the control system that enables the robot to smoothly operate in different states. The claw is controlled by one PID controller model that is simulated in Simulink. The code in the MCU and the control system were designed with the idea of achieving the RCGs stated in table
1. The code compilation is done with the Arduino IDE and the selected MCU is the ESP32-Wroom-32. We created our PID with the input and output be based on the position of the
Part one of this paper indicates the five RCGs selected and maintained throughout the project term. Part two discusses the control system model and design and part three discusses the MCU and code portion to achieve our RCGs.
Nomenclature
PID | Proportional, Integral, Derivative controller
RCG | Requirement, Constraint, Goal
MCU | Microcontroller Unit

### 1. RCGs

For the optimal controls portion of this project, we require the claw to move with precision and smoothly to each of its states (origin, grasping, moving, and releasing). With this information in mind, the following RCGs are made to open and close the claw accurately without overshooting and with as minimal settling time.
RCGs | Requirement | Constraint | Goal
Settle Time | Settle time must be less than 2s | Settle time can’t be too fast that it will cause something to break | Minimize settle time as much as possible
Overshoot | Overshoot must be less than 10% | Cannot run faster than the control frequency | Minimize overshoot as much as possible

ISR | ISR frequency must be smaller than 12x the most dominant pole | Frequency cannot be faster than 10x the most dominant pole | Frequency needs to be as close to 10x the most dominant pole
State Indication | Code must exemplify what state of the design is in at a 1Hz frequency | Timer needs to have enough bits to run at 1Hz | Code needs to indicate all states as visible as possible
Rise time | Rise time must be less than 1s | Rise time can’t be faster than settling time | Minimize rise time as much as possible

Table 1: RCGs for the optimal control portion

### 2. Controller System

For our control system, we have two inputs that perform at different times, one with the goal to close the claw and one with the goal to open the claw. This feeds into our PID with K!,K", and K# parameters that is then fed into the second order amplifier. After this, we feed the signal into our electrical admittance then apply a K$ gain to it and apply a 60-ratio gain value, as the gear ratio is 60 to 1. The electrical admittance outputs a torque value which becomes the input of our mechanical admittance subsystem and outputs speed. This signal gets fed back into the admittance motor loop and a torque constant gain K%.

### 2.1 Amplifier

To enable the motor to have enough torque and power to perform its role, we use an H-bridge. We obtained our second order amplifier transfer function from using an oscilloscope to obtain data and used the MATLAB script in Appendix A to obtain the transfer function shown below (1). The step response graph of this model is also shown down in Appendix B.

(1)

### 2.2 Motor

Our electrical admittance was modelled by measuring the inductance and resistance of the motor. Through the electrical admittance model, we convert voltage to current. The represented transfer function is shown below in (2).

&

'()* = | & +.++&--.()/.&0/ (2)

### 2.3 Tuning

Combining all of these in Simulink we can get the corresponding system shown in Figure 1.

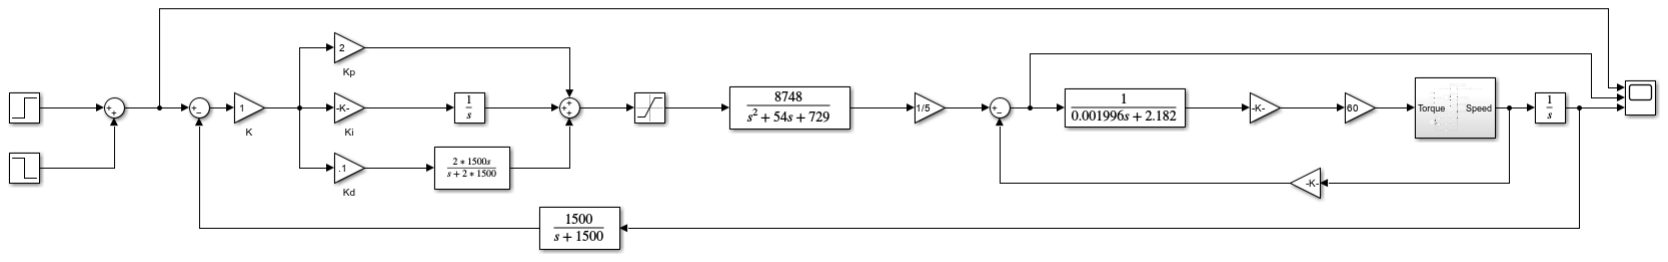
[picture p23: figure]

Figure 1: Control system of claw

Tuning the PID to the desired move in Figure 1, I use the method of manually tuning the PID following the steps noted down in my references [2]. I first set the integral and derivative gains to zero before I change the proportional gain to a small oscillating wave. Then, I increase the integral gain a little bit to stabilize the proportional gain without too much overshoot. Then, I increase the derivative gain to dampen the signal and then increase the proportional gain again until my signal settles at the input line. This results in the red line shown in Figure 2. I use the method of manually tuning the PID incorporating non-linearities of the mechanical model can help achieve more accurate gains and because I did not receive the mechanical admittance values to replace the subsystem with a transfer function.

Overall, combing all the components we use in this model, we were able to tune the graph to fit into our RCGs with less than 10% overshoot and roughly 0.5s of settle time. Rise time also takes about 0.5s.

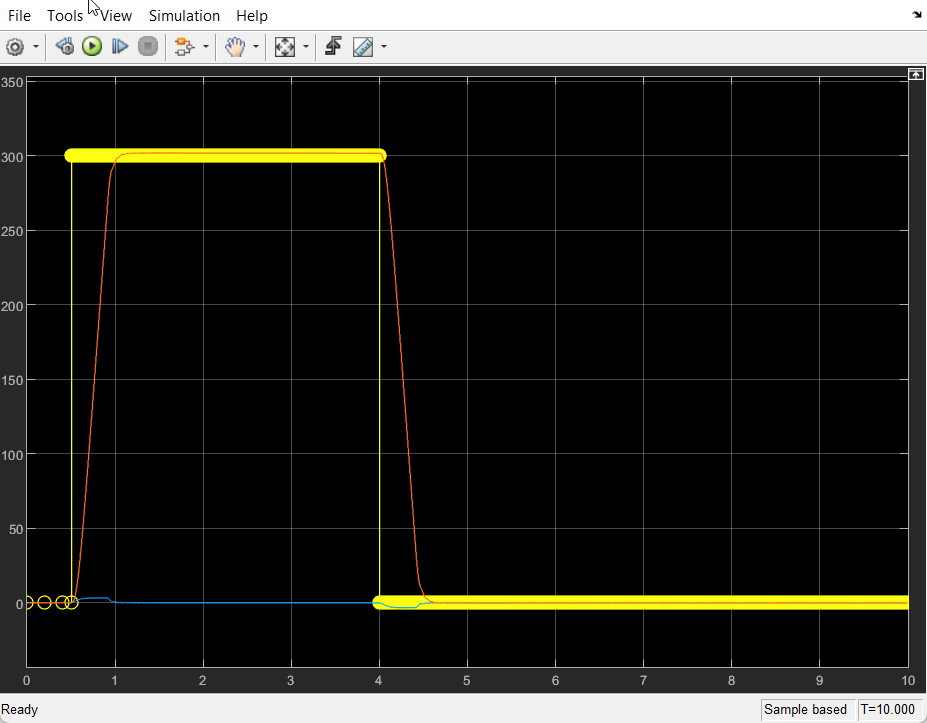
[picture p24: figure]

Figure 2: PID Position output

### 2. Microcontroller

### 2.1 MCU Selection

The selected MCU is an ESP32-WROOM-32. It has a 32 pin layout with the flexibility to allow any GPIO output pins to be made into PWM pins. We selected this MCU to allow us to run more ISRs as there are 2 hardware timers available with 64 bit each.

### 2.2 ISR

We run one internal ISR for the PID, one external ISR to open the claw when the metal sensor detects a magnet. The frequency for this ISR is set to be 10x the most dominant pole of our control system in Figure 1, 1.5kHz or more. So using the code in Figure 3, I configure the frequency of our motor PID for the ESP32 to be roughly 15kHz. The overall clock frequency of the ESP32 is 80MHz. Taking this into mind, we first need to use a prescalar of 1 and a timer overflow of 5333 to have our PID ISR run at 15kHz.

Figure 3: PID frequency configuration

### 2.3 State Indication

To clearly identify the state of the system, I ran the LED at a 1Hz frequency as shown in the code below in figure 4. I run the led at different PWMs at each state, 70% at its normal state, 10% while closing, 40% while travelling at 100% while opening the claw. I model the output of the LED to make sure the PWM at each state corresponds correctly and it can be seen below in Figure 5.


Figure 4: Code for state indication


Figure 5: PWM model of LEDs 70 -> 10 ->40 ->100 References
[1] ESP32 Series Datasheet, 2023, https://www.espressif.com/sites/default/files/documentation/esp32_datasheet_en.pdf
[2] Driver PID Settings, 1999-2023, https://www.thorlabs.com/newgrouppage9.cfm?objectgroup_id=9013

Appendix:

Appendix A:


Appendix B:


Appendix C:

/* IMPORTED LIBRARIES */
#include <PID_v1.h>

#include <HCSR04.h>

/* MISC CONSTANTS */
#define PLDCOMM 10

#define MAXPULSE 16383 // 14-bit #define MOTORFREQ 30000

#define LEDFREQ 1

#define PRESETPOINT 8544

/* PINS */
#define MOTORPIN 10

#define IN1PIN 11

#define IN2PIN 12

#define IN1CHANNEL 1

#define IN2CHANNEL 2

#define LEDPIN 32

#define LEDCHANNEL 0

#define SENSOR2PIN 33

#define ECHOPIN 26

#define TRIGGERPIN 27

/* LED DUTY CYCLES */
#define TENPERC 6554

#define FORTYPERC 26214

#define ONEHUNPERC 65536

#define SEVENTYPERC 45876

/* GLOBAL VARIABLE DECLARATION */ double setPosition;
double input, output;
double Kp = 0.5, Ki = 0.1, Kd = 0.5; int pulse = 0;
int pulseOverflow = 0;
bool home = true;
bool flag = false;

/* INITIALIZE PID TIMER, MOTOR PID MODEL, AND SENSOR */ hw_timer_t *pidTimer = NULL;
UltraSonicDistanceSensor distanceSensor(TRIGGERPIN, ECHOPIN); PID motorPID(&input, &output, &setPosition, Kp, Ki, Kd, DIRECT);

void setup()
{
Serial.begin(9600);

pinMode(MOTORPIN, OUTPUT); pinMode(IN1PIN, OUTPUT);
pinMode(IN2PIN, OUTPUT);
pinMode(SENSOR2PIN, INPUT);

// LED states at 1Hz PWM and 16 bit resolution at channel 0 ledcAttachPin(LEDPIN, LEDCHANNEL);
ledcSetup(LEDCHANNEL, LEDFREQ, 16);

// Motor PWM setup 30kHz at channel 1 and 2 at 8 bit resolution ledcAttachPin(IN1PIN, IN1CHANNEL);
ledcSetup(IN1CHANNEL, MOTORFREQ, 8);
ledcAttachPin(IN2PIN, IN2CHANNEL);
ledcSetup(IN2CHANNEL, MOTORFREQ, 8);

// ISRs
pidTimer = timerBegin(2, 1, true); // pidTimer number 2, divider = 1 bc no prescalar needed
timerAttachInterrupt(pidTimer, &PID, true);
timerAlarmWrite(pidTimer, 5333, true); // Every 15Khz PID will run 80MHz/5333 = 15Khz
motorPID.SetMode(AUTOMATIC);

attachInterrupt(digitalPinToInterrupt(SENSOR2PIN), openClaw, RISING);

}

void loop()
{
ledcWrite(LEDCHANNEL, SEVENTYPERC); digitalWrite(MOTORPIN, LOW);
float distance = distanceSensor.measureDistanceCm();

Serial.print("Distance from object: "); Serial.println(distance);

if (distance <= 15.0 && distance >= 0 && home) {
closeClaw();
}
}

void closeClaw()
{
Serial.println("Entering closeClaw state"); ledcWrite(LEDCHANNEL, TENPERC); setPosition = 8544;
flag = true;

// Initialize motor pin without PWM digitalWrite(MOTORPIN, HIGH); ledcWrite(IN2PIN, 0);

// Start PID
home = false;
timerAlarmEnable(pidTimer);

// Should not get to this case, but goes to next state if PID > 30s delay(30000);

// Next state: Travel Claw
travelClaw();
}

void PID()
{
if (!home)
{
int pulseTemp = 0b0;
bool pin;

for (int i = 0; i < PLDCOMM; i++) {

// PIN D0 - D9 (D0-D9)
pulseTemp = pulseTemp << 1 | int(digitalRead(i));
}

Serial.print("Current pulse, prev pulse, overall pulse, max pulse: "); Serial.println(pulseTemp);
Serial.println(pulseOverflow);
Serial.println(pulse);
Serial.println(MAXPULSE);

// Motor running backwards
// case that pulse count overflows backwards from 200 -> 15950
// or motor goes backward 800 -> 400, chose 1000 as buffer as
// pulses should not be greater than that with PID ISR
if ((pulseTemp)*0.5 > pulseOverflow || (pulseOverflow - pulseTemp < 1000 && pulseOverflow - pulseTemp > 0))
{
pulse = pulse - (MAXPULSE + pulseOverflow - pulseTemp);
pin = IN2PIN;
Serial.print("Motor running backwards");
}
else
{
// Motor running forwards
// case if pulse is regularly larger or is less than prev pulse pulse = pulse + (pulseTemp - pulseOverflow);
pin = IN1PIN;
Serial.print("Motor running forwards");
}

pulseOverflow = pulseTemp;
input = pulse;
motorPID.Compute();

ledcWrite(pin, 255 * abs((setPosition - output) / PRESETPOINT));

Serial.print("New overall pulse, PID output: "); Serial.println(pulse);
Serial.println(output);

// PID settles close enough
if (output <= setPosition + 1 && output >= setPosition - 1) {
timerAlarmDisable(pidTimer);

if (flag)
{
travelClaw();

}
else
{
openClaw();
}
}
}
}

void travelClaw()
{
Serial.println("Entering travelClaw state"); home = true;
ledcWrite(LEDCHANNEL, FORTYPERC);

// Motor stop spin, sanity check ledcWrite(IN1PIN, 0);
ledcWrite(IN2PIN, 0);

// Should not get to this case, but goes to next state if // it doesn't see sensor for > 30s
delay(30000);

// Next state: openClaw()
openClaw();
}

// Last state (ISR):
void openClaw()
{
Serial.println("Entering openClaw state"); // ISR sense
ledcWrite(LEDCHANNEL, ONEHUNPERC); setPosition = 0;
flag = false;

ledcWrite(IN1PIN, 0);

// Start PID
home = false;
timerAlarmEnable(pidTimer);

// Should not get to this case, but goes to next state if PID > 30s delay(30000);

// Next state: Home
home = true;
}

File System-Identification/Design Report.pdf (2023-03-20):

## Ball Hopper – System Identification

White-Paper | Updated – March 19, 2023

Jaydon Alexis, Group Portugal, ECE, University of BC, Vancouver, BC, Canada

Abstract

A custom robotic claw was designed and simulated in SolidWorks and Simscape for the purpose

of creating a tennis ball hopper. The claw is designed with 1 DOF for grasping and releasing

tennis balls and similar objects but is otherwise human driven. The design process involved

multiple concept sketches, drawn at reduced scale to characterize the mode of operation and

inverse kinematics of each design. A detailed CAD model of the chosen design was created in

SolidWorks and FEA was performed on relevant components to ensure that they satisfied stress

constraints. Upon completion of the CAD model, it was exported to Simscape for the design of

the PID controller in the Controls portion of the project.

The first section of this paper outlines the relevant requirements, constraints and goals for this

subsystem of the project that guide the design process. The second section describes

dimensions and inverse kinematics of the hopper in two dimensions. A three-dimensional

representation of the claw in SolidWorks is explored in the subsequent section as well as the

aforementioned stress analyses. The fourth section reviews the various calculations that were

conducted to inform selection of the motor and mechanical components such as bearings and

the lead screws in addition to parameters for the Simscape model. Finally, the last section

details the results obtained from the integration of the mechanical claw assembly with the

overall system model.

Nomenclature

AL | Arm Length
CAD | Computer Aided Design
DOF | Degrees of Freedom
FEA | Finite Element Analysis
OTS | Off the Shelf
RCG | Requirement, Constraint, Goal
SR | Shaft Radius

### 1. RCG Identification

The RCGs that guide the design process for the mechanical subsystem are shown in Table 1.1 below. They will be referenced in discussions throughout the body of the report.

Issue | Requirement | Constraint | Goal
Claw Load | The claw must be able to lift 5 Newtons of load | The lifting force is friction | Maximize the load that can be lifted by the claw
Claw Gape | The distance between the tips of the claw arms which contact the object must be at least 7 cm when in the open position | The moving hub must not exceed 1 inch of linear travel in closing and opening the claw | Maximize the distance between the tips of the claw arms which contact the object when in the open position
Component Stress | None of the claw components must exceed the maximum stress rating for the material they were constructed with at any location | No component should have a thickness greater than 30 mm at any point for the sole purpose of stress reduction | Minimize the stress in each of the claw components
Claw Weight | The claw must have a combined mass less than 750 g | The claw must be large enough to allow the average player to comfortably operate it while attempting to hop balls | Minimize the combined claw mass
Volume Occupancy | The gear assembly and electrical subsystem must fit within a volume of 900 cm³ | The gearbox assembly and the electrical subsystems must exist in isolated sections of the occupied volume | Minimize the volume occupied by the gear assembly and the electrical subsystem

### 2. Dimensions & Kinematics

Before modeling the hopper, dimensional constraints had to be established in accordance with

the previous section. The claw needed to be long enough to allow a player to grasp the tennis

ball of approximately 6.8 cm diameter without having to bend down excessively. Furthermore,

the claw uses a lead screw mechanism, so the bottom of the lead screw needed to have a

certain vertical clearance from the top of the ball when grasped. Given this information, the

following dimensions were qualitatively selected to provide a reasonable trade-off between

the moment of inertia and efficiency of motion. Figures 2.1 and 2.2 show drawings of the

inverse kinematics for the claw in its fully opened and fully closed states, respectively, for a

single arm of the claw.


Figure 2.1. Inverse Kinematics in the Open Position


Figure 2.2. Inverse Kinematics in the Closed Position

### 3. Three-Dimensional SolidWorks Model & Stress Analysis

### 3.1 Model Features

Using the validated dimensions from the inverse kinematics of the selected claw model design

in the previous section, several components were individually modeled before being

compounded together in an assembly. These include the claw arms, a fixed and a moving hub,

connecting rods to link the moving hub to the arms, a lead screw and its associated nut, the

motor and a gearbox. The claw assembly is shown in Figure 3.1 below.


Figure 3.1. Claw Assembly

The lead screw is the component that allows the transformation of the rotational motion of the

motor to the linear motion of the moving hub. The lead screw is coupled to the motor shaft via

a reduction gear box. As the screw rotates, the threads of the screw and its nut shown in Figure

3.2. interact to exert a vertical thrust force on the nut and the moving hub by extension.

Through the vertical motion of the moving hub, opening and closing of the claw can be

achieved through the connecting rods shown in Figure 3.3 that are attached to the arms.


Figure 3.2. Lead Screw & Nut | Figure 3.3. Hub-Arm Coupling via Connecting Rod

The gearbox features a 60:1 gear ratio which is accomplished within a confined space using a

worm gear mechanism as shown in Figure 3.4. This reduces the torque required by the motor

to lift the arms as well as the tennis ball once it has been grasped as described in the third

section which allows us to achieve a reasonable speed of linear motion for the moving hub

using the Pololu 12V motor the specifications of which can be found in the Pololu motor catalog

[1]. The gearbox housing also accommodates the electrical subsystem for the claw, including

PCBs and cables as shown in Figure 3.5.


Figure 3.4. Worm Gear Assembly | Figure 3.5 Gearbox & Electrical Component Housing

### 3.2 Stress Analysis

Stress analysis was conducted on the claw arms to ensure that the structural integrity of the

PLA material used to fabricate the claw would not be compromised in the case of maximum

torque supplied by the motor. A force of 0.79 N was applied to the end of the claw arm in the

simulation environment which corresponds to the maximum expected normal force at that

location as outlined in section three when it makes contact with the ball. The results of the FEA simulation are shown in Figure 3.6. Given that the tensile strength of the PLA material used to

manufacture the claw is about 50 MPa, it is evident that the claw arm design is robust with the

maximum stress being 0.22 MPa, corresponding to a safety factor of approximately 220.


Figure 3.6. Claw Arm FEA Simulation

A similar process was performed for the connecting rods that link the claw arms with the

moving hub. The result of the simulation is shown in Figure 3.7 and it shows a safety factor of

approximately 29 suggesting that the connecting rod design is also robust.


Figure 3.7. Connecting Rod FEA Simulation

### 3.3 Cost Analysis

An estimate for the cost price of the components of the claw assembly are shown in Table 3.1

below. All prices shown are in USD.

Component | Price (USD)
Steel Worm Gear (x1) | $13.56
Plastic Worm Gear (x1) | $17.24
5 mm Ball Bearing (x2) | $34.96
Carbon Steel Acme Hex Nut (x1) | $3.90
Carbon Steel Acme Lead Screw (x1) | $13.80
Needle-Roller Bearing (x1) | $6.50
Zinc Yellow-Chromate Plated Hex Head Screw (x1) | $11.65
Washdown Clamping Shaft Collar (x1) | $10.40
¾ inch Ball Bearing (x2) | $11.78
Medium-Strength Steel Hex Nut (x1) | $15.94
Dowel Pin (x4) | $50.72
18-8 Stainless Steel Hex Head Screw (x1) | $5.76
Steel Hex Nut (x1) | $2.62
Set Screw Shaft Coupling (x1) | $15.95
Pololu 12V Motor | $26.75
3D Printing Material (PLA) | $40.00
TOTAL | $281.53

Table 3.1. Cost Report for Claw Assembly

### 4. Torque & Force Calculations

### 4.1 Gear Ratio

Due to the relatively large inertia of the claw assembly, a greater torque than that which could

be directly supplied by the 12V Pololu motor was required so a gearbox was included to

multiply its torque. However, a compromise needed to be made between torque and rotational

speed of the lead screw which decreases as the torque increases. To determine the optimum

gear ratio, the calculations described below were performed. The variables for the equations

used in the calculations are defined in Figure 4.1.


Figure 4.1. Equation Variables

The force and torque balance equations for the system are as follows:

P1x + (P2)(cos θ) – FN = 0 | (1)
P1y – (P2)(sin θ) – (FN)(μ) = 0 | (2)
(FN)(y) = (P2)(x) | (3)
(3)(μ)(FN) – FW = 0 | (4)

The quantities x and y were obtained using the measure tool within SolidWorks. μ, the

coefficient of friction, was determined using a standard table of coefficients [2].

The thrust required to displace the moving hub was obtained by taking the vertical component

of the quantity P2 and multiplying it by 3 for each of the three fingers. This thrust can be

converted to a required torque using the following equations for an acme lead screw:

T =

(F)(Dp)
2

(cos ∅)(tan α)+f
cos ∅−(f)(tan α)

(5)

tan α =

π
Dp

(6)

where T is the torque, F is the thrust, Dp is the pitch diameter, ∅ is the thread angle which is

14.5o
in this case, α is the lead angle and f is the coefficient of friction which was obtained from

a standard table for lubricated carbon steel-carbon steel contact [2].

The result for required torque suggested that a gear ratio of 60:1 was sufficient for our

purposes.

### 4.2 Lead Screw

The no load speed of the motor is approximately 10000 revolutions per minute. Therefore, with

a speed ratio of 60:1, the rotational speed of the lead screw would be about 166 revolutions

per minute. The inverse kinematics of the claw allow a linear range of motion for the moving

hub of about 1 inch. Thus, to allow for a reasonable linear speed of travel for the moving hub, a

lead screw was selected with a linear distance of 1 inch per turn. This also translates to simpler

control system design since only one rotation of the lead screw needs to be considered.

### 4.3 Material Selection

The torque to actuate the claw assembly is directly proportional to its inertia which is

proportional to the mass of its individual components. Therefore, low density materials are

preferred but one must make a compromise between material weight and material strength

since less dense materials are usually more prone to failure.

The solution pursued in this case was to 3D print the majority of the main claw components

including the arms, connecting rods, shafts and hubs with PLA, which has a relatively low density of 1.24 g/cm³ which was found in a material density chart [3]. but they were made to

have a certain minimum level of thickness to avoid the risk of failure. For components that were not 3D printed, specifically the purchased components, Aluminium was the preferred material due to its lightweight (2.7 g/cm³
) and rigid properties.

### 5. Simscape Model

The completed SolidWorks model was exported to Simscape so that the gains of the PID

controller could be tuned appropriately taking the entire system model into account. The

gearbox was not included in order to increase the simplicity and accuracy of the model, but

scaling was introduced where necessary to account for such an optimization. The model within

the Simscape environment is shown in Figure 5.1 in its open position.


Figure 5.1. Simscape Model View

To close the claw, the moving hub moves to the free end of the lead screw which corresponds

to a linear distance of about 1 inch. Torque is applied to the other end of the lead screw and is

scaled by the gear ratio to account for the torque amplification of the gearbox while the

angular speed of the lead screw is sensed by the controller. The speed is scaled by the gear

ratio as well since the lead screw rotates at a slower rate than the motor shaft. The exported

Simscape model is shown in Figure 5.2 while the complete system model is shown in Figure 5.3.


Figure 5.2. Exported Simscape Model

Figure 5.3. Complete System Model

Most of the joints are revolute joints since the model contains mainly hinge joints which rotate

about each other. A damping coefficient was applied to all revolute joints corresponding to the

PLA-PLA coefficient of friction. A lead screw joint was created between the lead screw and its

associated nut to allow for the torque applied to the screw to translate to the linear motion of

the nut. Damping associated with carbon steel-carbon steel contact was applied at this joint.

References

[1] Pololu motor catalog, (2023), https://www.pololu.com/product/2821
[2] Friction Coefficients and Calculator, (2023), https://www.engineeringtoolbox.com/friction-

coefficients-d_778.html (https://www.engineeringtoolbox.com/friction-coefficients-d_778.html)

[3] Density of Elements Chart, (2023), https://www.angstromsciences.com/density-elements-

chart (https://www.angstromsciences.com/density-elements-chart)

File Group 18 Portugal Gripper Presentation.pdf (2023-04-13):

2023-04-13

Ball Hopper: Gripper Robot; April 13, 2023; University of British; Columbia; ELEC 391; Leo Stocco; Group 18 - Portugal

Kerem Oktay - Idil Bil - Jaydon Alexis - Phi Lam

1

- Must be able to pick a
standard tennis ball
- Must carry the balls for at least a distance of 2
meters
- Must be compatible
with the given
interface unit

Requirements

- Cannot operate
without a permanent
magnet in the
destination

Constraints

- Maximize the
distance balls can be
carried
- Minimize the
operation time

Goals

2

System ID – Range of Motion


Inverse Kinematics for our Gripper
- An undefined sketch was drawn to characterize the range of motion and orientation for the gripper
- This allows us to perform motion planning more efficiently than doing calculations by hand
- Only the "open" and "close" states are shown here since these are the most important to consider

3

System ID - Lid


Multipurpose Lid
- Our mechanical interface is mounted at the top of the lid
- The tabs on each of the four corners of the lid are used to mount the rest of the assembly
- The shelves are used to house our Motor Driver, Pulse Counter & Motherboard PCBs
- A guiding bearing is also press fit into the bottom layer as shown in the left diagram

4

System ID - Gearbox


Gearbox Assembly
- It features a worm gear assembly with a 60:1 gear reductio n, multiplying the motor's torque sufficiently
- The bearings are used to reduce rotational friction and ensure smooth rotation of the driving and driven
- Tabs at the four upper corners are used to connect the gearbox and the rest of the claw assembly to the lid
- A support was placed at the side of the gearbox to mount the motor and correctly align it with the driver shaft

5

System ID - Claw


Claw Assembly
- The claw itself features three arms, three connecting rods, a lead screw and two hubs
- The upper hub in blue is used to mount the claw to the gearbox
- The lead screw transforms the rotational motion of the motor to the translational motion of the lower hub
- It lowers and raises the hub which in turn moves the fingers using the attached connecting rods
- The hub moves a distance of 0.125 inches per revolution of the lead screw

6

System ID - Full Gripper Assembly


Complete Gripper Assembly
- The components from the previous slides have been integrated together
- There are a few additional components including
- PCBs which have been placed inside of the lid
- The model for the tennis ball to be picked up
- The shaft collar that connects the lead screw to the driven shaft - Claw bolt supports between the gearbox and upper hub

7


System ID - Simscape Model

Simscape Simulation
- The Simscape model for the claw assembly is shown on the right while the model within the Simscape simulation environment is shown on the left
- Most of the model blocks are connected via revolute joints which represent rotational motion about the hinges of the claw assembly
- There is also a lead screw joint between the power screw and the lower hub to simulate the transformation from rotational motion to translational motion
- This subsystem was incorporated into our complete system model as a mechanical admittance

8

Analog Electronics - Motherboard Schematic


Motherboard PCB Schematic
- Esp32 devboard is used as the microcontroller as it provides enough pins and timers
- Ultrasonic sensor is used to detect the tennis ball to be picked up
- Hall effect sensor is used to detect the destination marker
- Predefined power and digital interface units are used
- On the PCB assembly MCU RST and STATE signals have been reworked to match the crossover in the given electrical interface

9

Analog Electronics - Motherboard


PCB Routing for the Motherboard
- A two-layer PCB is designed for the Motherboard circuit
- All the peripherals are oriented towards the left side for easy access
- Red wires show the wiring on the top layer, while the blue wires show the wiring on the bottom layer

Photo of the Assembled PCB
- A Voltage regulator is used to supply regulated 5 V to necessary pins
- J2: It is the connector for the power of the Motor Driver
- J3: It is the connector for the control signals of the Pulse Counter
- CN1: It is the connector for the control signals of the Motor Driver

10

Analog Electronics – Level Shifter


Rework on a Perf Board
- Level shifters are used to convert 3.3 V signals of the microcontroller to 5 V signals for the Pulse Counter
- The level shifters are also bidirectional, allowing us to both read and write signals when necessary

11

Analog Electronics - Motor Driver Schematic


Motor Driver PCB Schematic
- L298 IC is used as the Motor Driver
- 4 fly back diodes are used to provide a path for the current to dissipate when the motor switches from on to off
- MOTIN1 and MOTIN2 signals are used to control the direction and speed of the motor

12

Analog Electronics - Motor Driver


PCB Routing for the Motor Driver
- A two-layer PCB is designed for the Motherboard circuit
- 1.2 mm width traces were used to carry current to the motor because they can withstand around 3 Amps, which was the max current rating we expected
- Control and motor power signals were separated onto different parts of the board as much as possible to reduce risk of cross talk

Photo of the Assembled PCB
- Connectors from left to right are: the motor, Pulse Counter board and Motherboard
- The connector on the bottom right is for powering up the Motor Driver

13

Digital Electronics - Pulse Counter Schematic


Pulse Counter PCB Schematic
- 3 20-pin DIP Sockets are used to mount HCTL-2022 and PLDs
- Crystal (XTAL) is used to provide necessary clock signal to HCTL-2022
- 1k Ohm pull-down resistors are used to ensure signals become low voltage properly and reduce noise
- External connectors are used to wire between boards

14

Digital Electronics - Pulse Counter


PCB Routing for the Pulse Counter
- A two-layer PCB is designed for the Pulse Counter circuit
- DIP Sockets are used to provide easy access to ICs if needed to take apart
- SMD resistors are used to minimize the occupied space

Photo of the Assembled PCB
- ICs from left to right are as follows: PLD (4-1 MUX) / HCTL-2022 / PLD (4-1 MUX)
- J5: It is the connector for Control and Output signals of HCTL-2022 and MUXs
- CN1: It is the connector for Encoder A/B Signals coming from the Motor Driver board

15


Digital Electronics - Pulse to Angle Conversion

Algorithm to Read and Convert Pulse Count to Degrees
- getPulseCount function sets SEL1 and SEL2 signals to read byte number "i"
- getByte function sets S1 and S2 signals to read a bit pair "j"
- 1 byte = 8 bits -> getByte loops 4 times
- Pulse Count is 32-bit value, 32 bits = 4 bytes -> getPulseCount loops

### 4 times

16

Optimal Control – Software Implementation


ESP32-Dev | Ultrasonic Sensor | Hall Effect Sensor

ESP32
- All the pins give flexibility to use PWM, 32 pin layout
- PWM easy to configure frequency and resolution to blink state
- Fit requirement for ISR timer at frequency that we're using

State
- Homing and then 4 different states
- "Close" + "Open" claw use PID tuning
- Sensors used to move between states
- PID also used to move between states

17

Proportional (Kp) = 0.22; Integral (Ki) = 0; Derivative (Kd) = 0

Optimal Control – PID ISR and Tuning

P-Controller
• Helps increase to set point
• Increase until oscillates, decrease rising time

I-Controller
• Helps decrease offset
• Could cause overshoot if increased too much

D-Controller
• Decrease overshoot / damping

## Gripper Demo


Videos for the Project

- Motor moving the fingers: https://drive.google.com/file/d/1yS_-Fr6xO_KhF4LMuMfDDbp4060NnIY1/view?usp=sharing
- The control system working before integration, with
sensors: https://drive.google.com/file/d/1pgXOPBrIMusSZi8hItNfwTtvf7tGX0xt/view?usp=sharing

19

Thank you for listening!; April 13, 2023; University of British; Columbia; ELEC 391; Leo Stocco; Any questions?

Kerem Oktay - Idil Bil - Jaydon Alexis - Phi Lam

20

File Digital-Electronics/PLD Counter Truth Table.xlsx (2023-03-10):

Truth Table |  |  |  |  |  |  |  |  |  |  |  | Truth Table
clk | q9 | q8 | q7 | q6 | q5 | q4 | q3 | q2 | q1 | q0 |  | clk | q3 | q2 | q1 | q0
 |  |  |  |  |  |  |  |  |  |  | 0 pulse | 0 | 0 | 0 | 0 | 0
 |  |  |  |  |  |  |  |  |  |  |  | 1 | 0 | 0 | 0 | 0
 |  |  |  |  |  |  |  |  |  |  | 1 pulse | 0 | 0 | 0 | 0 | 1
 |  |  |  |  |  |  |  |  |  |  |  | 1 | 0 | 0 | 0 | 1
 |  |  |  |  |  |  |  |  |  |  | 2 pulse | 0 | 0 | 0 | 1 | 0
 |  |  |  |  |  |  |  |  |  |  |  | 1 | 0 | 0 | 1 | 0
 |  |  |  |  |  |  |  |  |  |  | 3 pulse | 0 | 0 | 0 | 1 | 1
 |  |  |  |  |  |  |  |  |  |  |  | 1 | 0 | 0 | 1 | 1
 |  |  |  |  |  |  |  |  |  |  | 4 pulse | 0 | 0 | 1 | 0 | 0
 |  |  |  |  |  |  |  |  |  |  |  | 1 | 0 | 1 | 0 | 0
 |  |  |  |  |  |  |  |  |  |  | 5 pulse | 0 | 0 | 1 | 0 | 1
 |  |  |  |  |  |  |  |  |  |  |  | 1 | 0 | 1 | 0 | 1
 |  |  |  |  |  |  |  |  |  |  | 6 pulse | 0 | 0 | 1 | 1 | 0
 |  |  |  |  |  |  |  |  |  |  |  | 1 | 0 | 1 | 1 | 0
 |  |  |  |  |  |  |  |  |  |  | 7 pulse | 0 | 0 | 1 | 1 | 1
 |  |  |  |  |  |  |  |  |  |  |  | 1 | 0 | 1 | 1 | 1
 |  |  |  |  |  |  |  |  |  |  | 8 pulse | 0 | 1 | 0 | 0 | 0
 |  |  |  |  |  |  |  |  |  |  |  | 1 | 1 | 0 | 0 | 0
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

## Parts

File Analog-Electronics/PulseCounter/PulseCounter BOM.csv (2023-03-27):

Comment | Description | Designator | Quantity | Man. Part Number
JST 5P-XH-V | Connector Header, XH Series, 5 Position, 2.50mm, Through Hole, Press-Fit, Solder, Natural | CN1 | 1
PLD 1 | Socket, DIP; 20Pins; Dual Leaf; Closed; Solder Tail; 0.31In.; Beryllium Copper; Gold | J1 | 1
PLD 2 | Socket, DIP; 20Pins; Dual Leaf; Closed; Solder Tail; 0.31In.; Beryllium Copper; Gold | J2 | 1
HCTL-2022 | Socket, DIP; 20Pins; Dual Leaf; Closed; Solder Tail; 0.31In.; Beryllium Copper; Gold | J3 | 1
JST B8B-XH-A (LF)(SN) | XH Series 6 Position 2.5 mm Pitch Through Hole Top Entry Shrouded Header | J5 | 1
1k | RP73 Series Thin Film Fixed Resistor 0805 Case 1kOhm +/-0.1% 0.25W +/-25ppm/degC | R1, R2, R3, R4, R5, R6, R7, R8, R9, R10 | 10
ECS International ECS-100AX-100 | Oscillator XO 1MHz ±100ppm TTL 55% 5V 4-Pin Thru-Hole Tube | XTAL | 1

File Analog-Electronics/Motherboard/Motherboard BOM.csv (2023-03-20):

Comment | Description | Designator | Quantity | Man. Part Number
0.1uF | CAP CER 0.1UF 50V 10% RADIAL | C1, C2 | 2
JST 5P-XH-V | Connector Header, XH Series, 5 Position, 2.50mm, Through Hole, Press-Fit, Solder, Natural | CN1 | 1
CUI SJ1-3545N | 3.5 mm Right-Angle Stereo Jack, 5 Pin PCB Mount, Non-Threaded | J1 | 1
JST B2B-XH-A | Conn Shrouded Header HDR 2 POS 2.5mm Solder ST Thru-Hole Box | J2 | 1
JST B8B-XH-A (LF)(SN) | XH Series 6 Position 2.5 mm Pitch Through Hole Top Entry Shrouded Header | J3 | 1
AJ-SR04M Ultrasonic Sensor | Ultrasonic Sensor Module, Rectangular, 3-5 V, Arduino Compatible, Posed Horizontally | SEN1 | 1
Hall Effect Sensor | Conn; Rect; Header; 3 Cir; PCB; MicroFit 3.0; Rt Angle; Single; SMT; w/Tab; Tin | SEN2 | 1
ESP32-DOIT-DEVKIT V1 - 30 pin | ESP32-DOIT-DEVKIT V1 - 30 pin | U1 | 1
Texas Instruments LM7805CT | LM78XX Series 5 V Fixed Output 1 A 3-Terminal LDO Voltage Regulator - TO-220 | VR1 | 1
CUI PJ-102A | 2.0 x 6.5 mm, 2.5 A, Horizontal, Through Hole, Tapered Pins, Dc Power Jack Connector | X1 | 1

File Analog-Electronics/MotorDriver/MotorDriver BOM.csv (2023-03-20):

Comment | Description | Designator | Quantity | Man. Part Number
100nF | CAP CER 0.1UF 50V 10% RADIAL | C1, C2 | 2
JST 5P-XH-V | Connector Header, XH Series, 5 Position, 2.50mm, Through Hole, Press-Fit, Solder, Natural | CN1, CN2 | 2
1N4005-T | 1.0 A Rectifier, 8 pF, 600 V, -65 to 150 degC, 2-Pin DO-41 Plastic, RoHS, Tape and Reel | D1, D2, D3, D4 | 4
JST B2B-XH-A | Conn Shrouded Header HDR 2 POS 2.5mm Solder ST Thru-Hole Box | J1 | 1
Molex 22-28-4060 | KK® 254 Breakaway Header, Vertical, 6 Circuits, Tin (Sn) Plating, Mating Pin Length 6.09mm | J2 | 1
STMicroelectronics L298HN | PMIC - gate/half-bridge gate drivers STMicroelectronics L298HN Inductive Bipolar Multiwatt 15 | U1 | 1

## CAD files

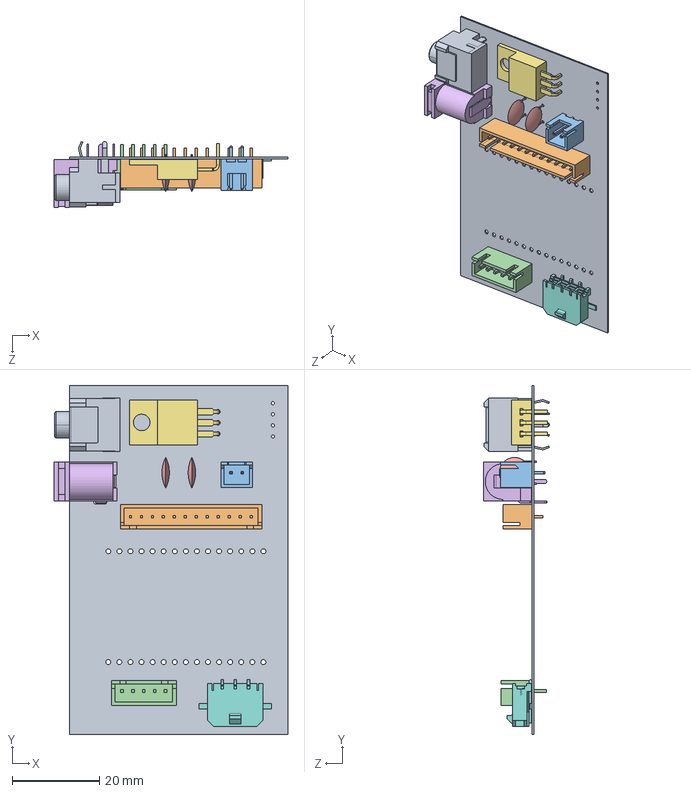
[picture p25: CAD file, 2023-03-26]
System-Identification/Motherboard.step.SLDASM
53.6 x 80.0 x 15.1 mm
CONN HEADER XH TOP 12POS 2.5MM JST.step
JST-XH - 2Pin v1.step
B5B-XH-A.step
User Library-Ceramic Disc Capacitor 0_2in pitch(1).step x 2
pj-102a.step
TO229.step
CUI_SJ1-3545N.step

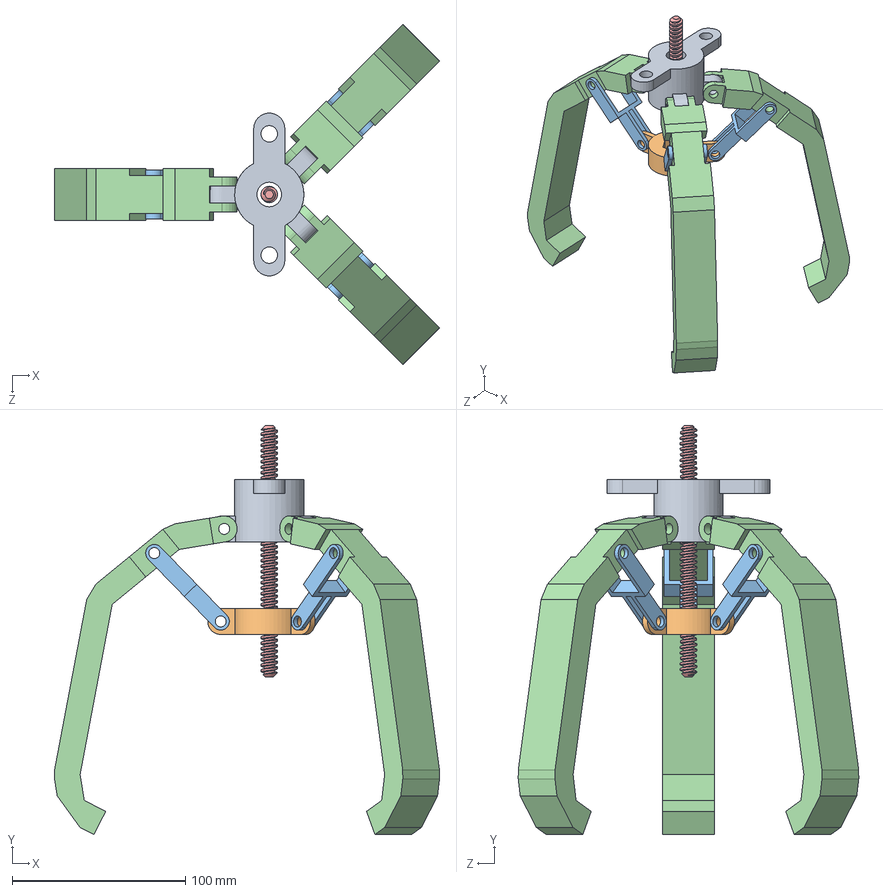
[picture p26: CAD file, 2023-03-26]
System-Identification/Gripper.SLDASM
222.2 x 236.0 x 196.5 mm
Hub
Nut
Connecting_Rod x 3
Fingertip x 3
Power_Screw

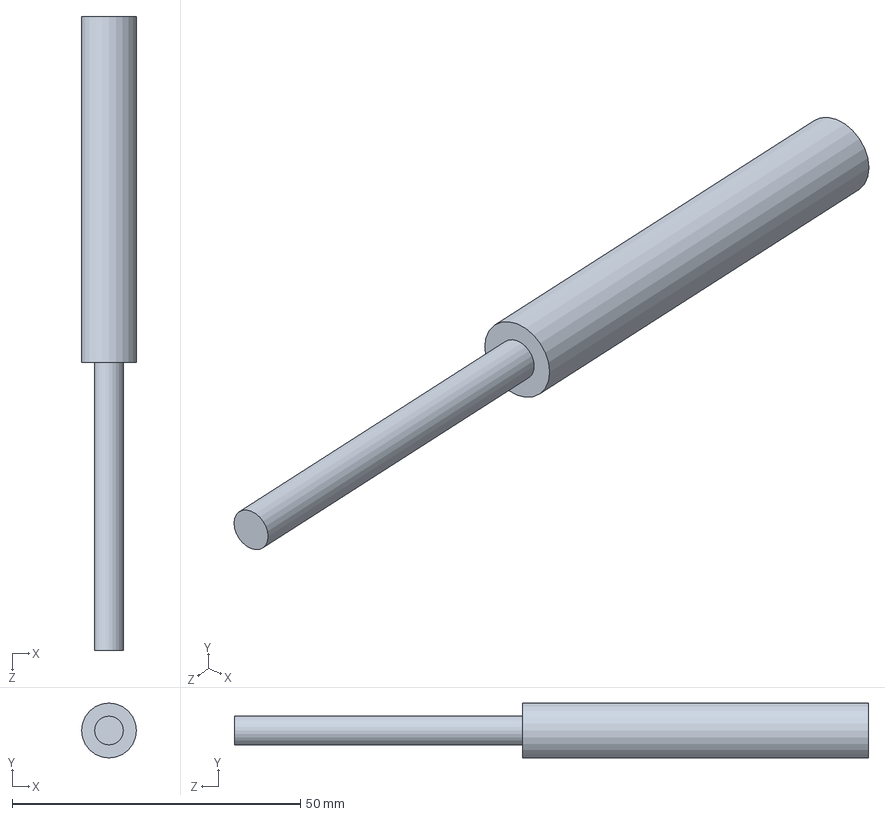
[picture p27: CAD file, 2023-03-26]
System-Identification/Driven.SLDASM
9.53 x 9.53 x 110.0 mm

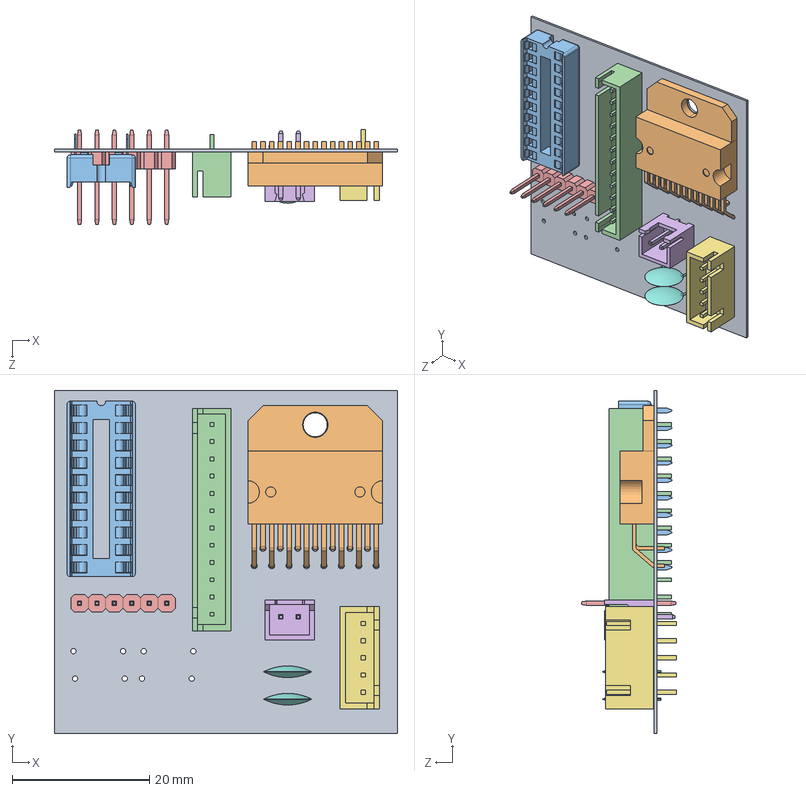
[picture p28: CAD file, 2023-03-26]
System-Identification/STEP_[No Variations] for DriverCCTPCB.CMPcbDoc.step.SLDASM
50.0 x 50.0 x 13.9 mm
User Library-Multiwatt15H.step
DIP300-skt-flat-20.step
CONN HEADER XH TOP 12POS 2.5MM JST.step
Header-SIP6.step
JST-XH - 2Pin v1.step
B5B-XH-A.step
User Library-Ceramic Disc Capacitor 0_2in pitch(1).step x 2

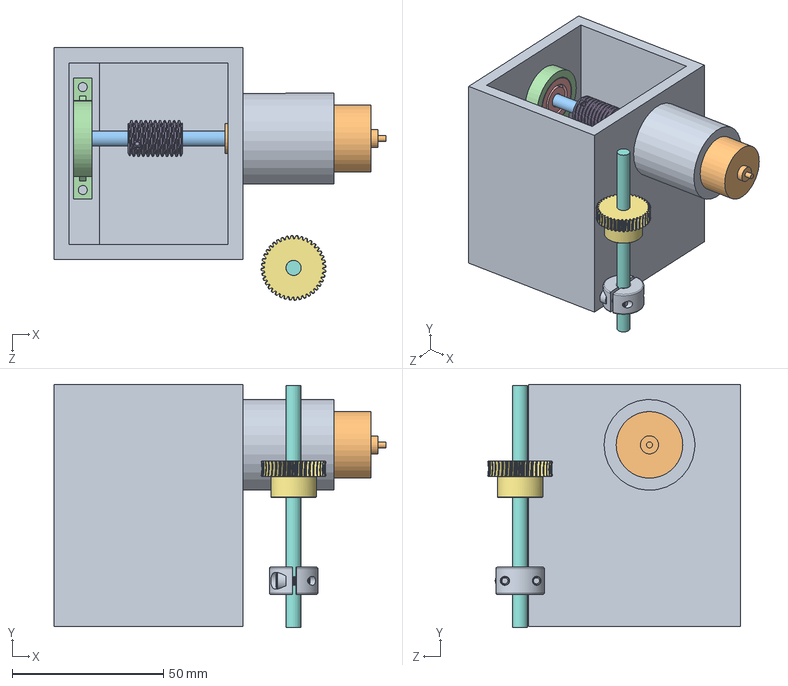
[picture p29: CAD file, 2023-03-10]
System-Identification/GearBox.SLDASM
109.7 x 80.4 x 83.4 mm
Motor
Adapter_I
Bearing_Housing
5972K197_Ball Bearing
57545K624_Steel Worm
4037N115_Plastic Worm Gear
Rod
9520T2_Clamping Two-Piece Shaft Collar

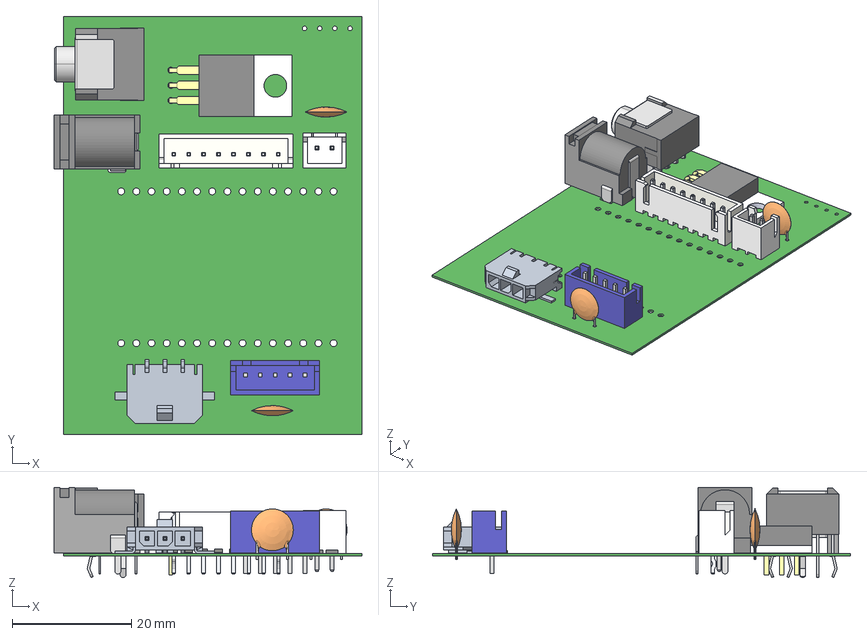
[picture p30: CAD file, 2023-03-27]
Analog-Electronics/Motherboard/Motherboard-step.step
51.6 x 70.0 x 15.1 mm
User Library-B8B-XH-A
JST-XH - 2Pin v1
B5B-XH-A
User Library-Ceramic Disc Capacitor 0_2in pitch(1) x 2
pj-102a
TO229
CUI_SJ1-3545N

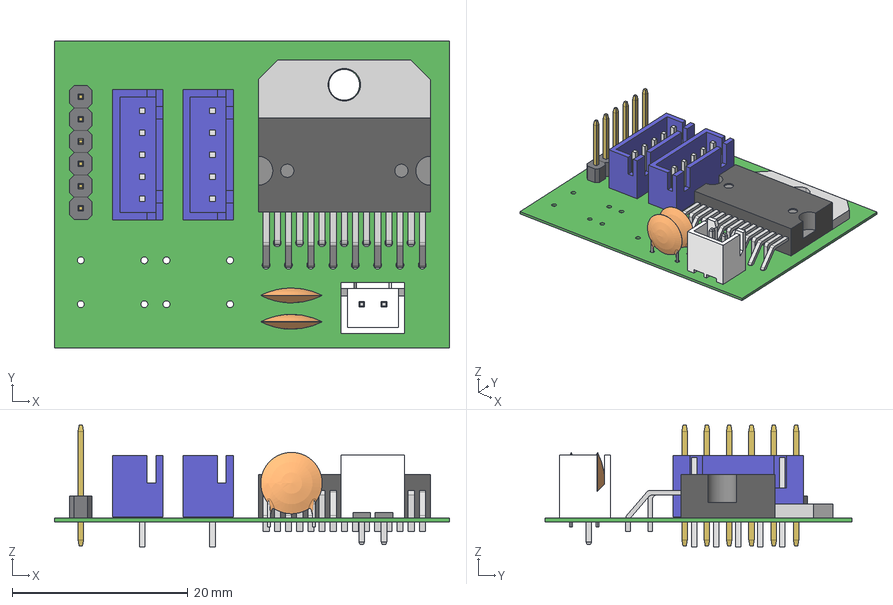
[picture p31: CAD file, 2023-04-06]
Analog-Electronics/MotorDriver/MotoDriver-step.step
45.0 x 35.0 x 13.9 mm
B5B-XH-A x 2
User Library-Multiwatt15H
Header-SIP6
JST-XH - 2Pin v1
User Library-Ceramic Disc Capacitor 0_2in pitch(1) x 2

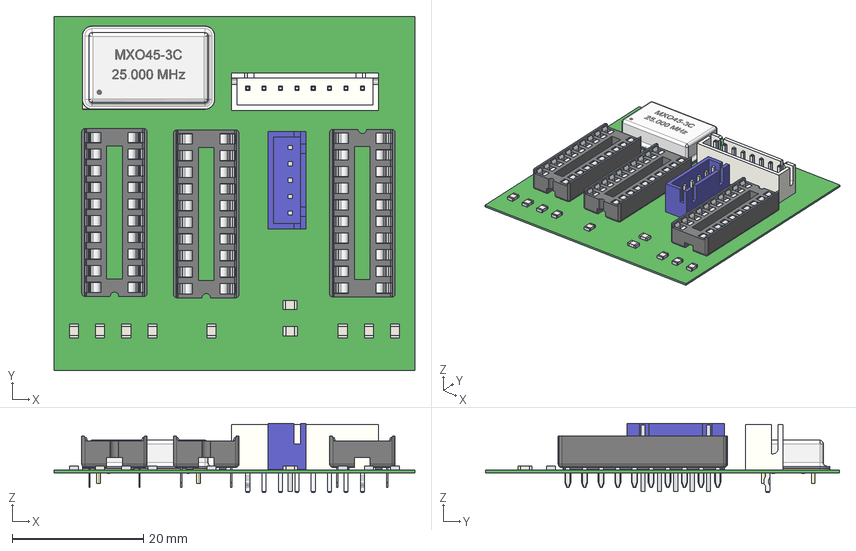
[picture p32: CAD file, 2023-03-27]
Analog-Electronics/PulseCounter/PulseCounter-step.step
55.0 x 54.0 x 10.5 mm
Extruded x 30
User Library-OSC_DIP-14
User Library-B8B-XH-A
DIP300-skt-flat-20 x 3
B5B-XH-A

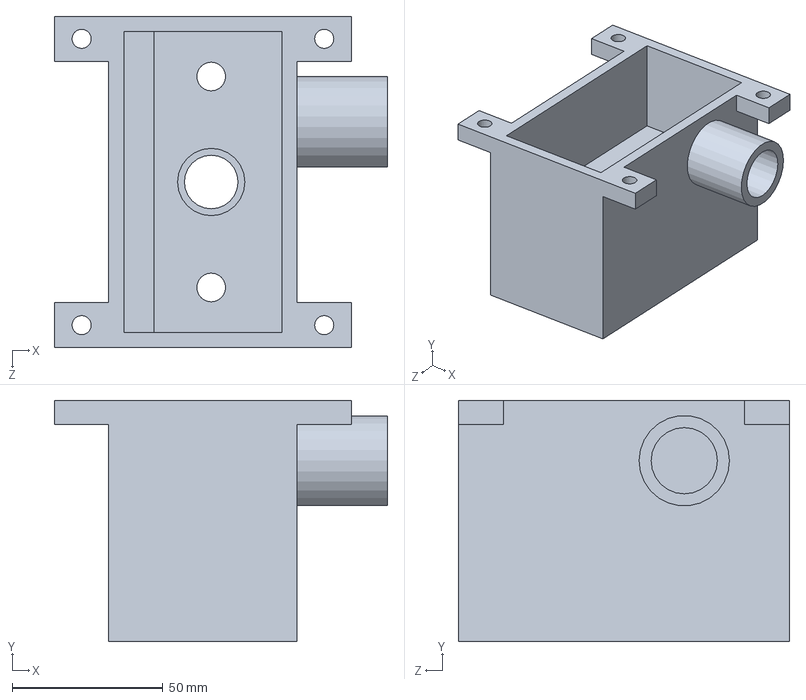
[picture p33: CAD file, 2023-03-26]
System-Identification/Box.SLDPRT
110.5 x 80.0 x 110.0 mm

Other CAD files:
System-Identification/C2.step.SLDASM
System-Identification/CN1.step.SLDASM
System-Identification/J1.step.SLDASM
System-Identification/Board.step.SLDASM
System-Identification/J2.step.SLDASM
System-Identification/C1.step.SLDASM
System-Identification/J3.step.SLDASM
System-Identification/CONN HEADER XH TOP 12POS 2.5MM JST.step.SLDPRT
System-Identification/JST-XH - 2Pin v1.step.SLDPRT
Analog-Electronics/Motherboard/Motherboard-parasolid.x_t
Analog-Electronics/MotorDriver/MotoDriver-parasolid.x_t
Analog-Electronics/PulseCounter/PulseCounter-parasolid.x_t
System-Identification/4037N115_Plastic Worm Gear.SLDPRT
System-Identification/4037N125_Plastic Worm Gear.SLDPRT
System-Identification/5709K901_Tapered-Roller-Bearing.SLDPRT
System-Identification/57545K624_Steel Worm.SLDPRT
System-Identification/5909K2_Needle-Roller Thrust Bearing.SLDPRT
System-Identification/5972K197_Ball Bearing.SLDPRT
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

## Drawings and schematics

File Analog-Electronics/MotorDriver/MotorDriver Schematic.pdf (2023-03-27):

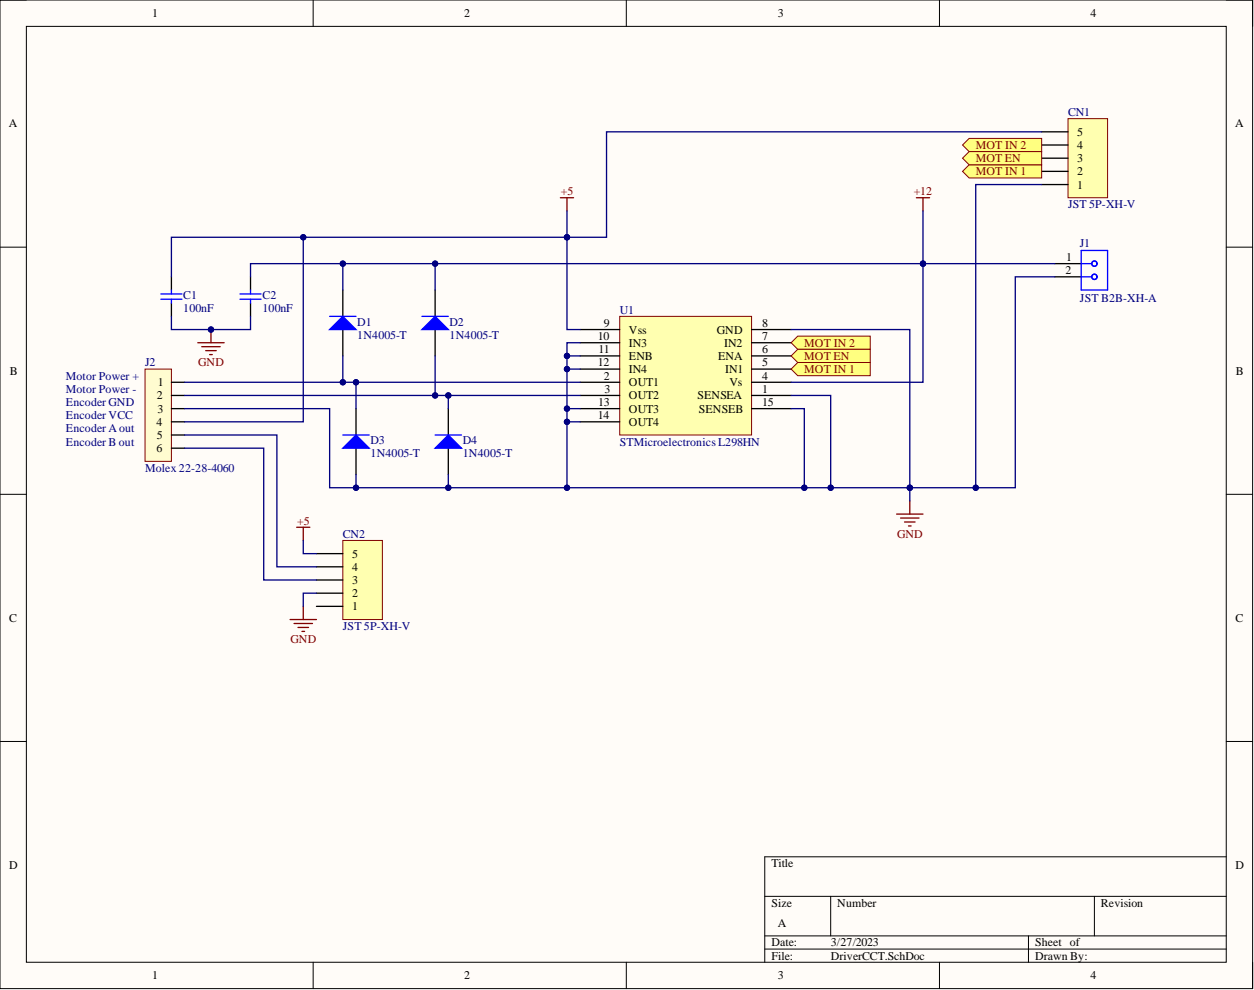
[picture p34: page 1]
der B; JST B2B-X

1 1 | 1 Vs 4 IN1 5 ENA 6 IN2 7 GND 8 5 SENSEA
1 0 | | MO T IN 2 MO T E N MO T IN 1

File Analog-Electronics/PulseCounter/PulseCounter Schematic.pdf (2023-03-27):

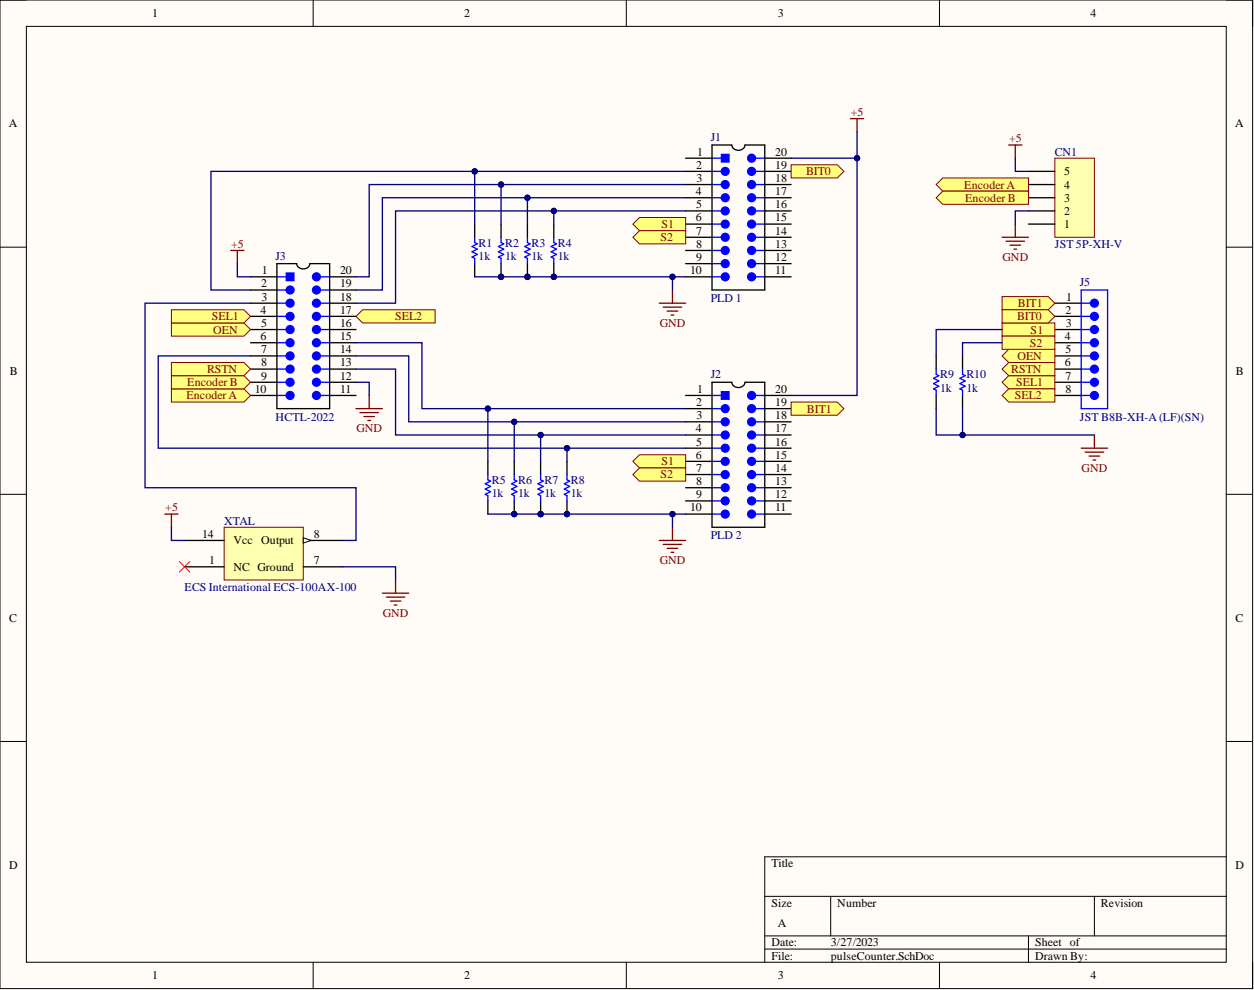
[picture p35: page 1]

JST B8B-XH-A (LF)(SN)

GND | | 4

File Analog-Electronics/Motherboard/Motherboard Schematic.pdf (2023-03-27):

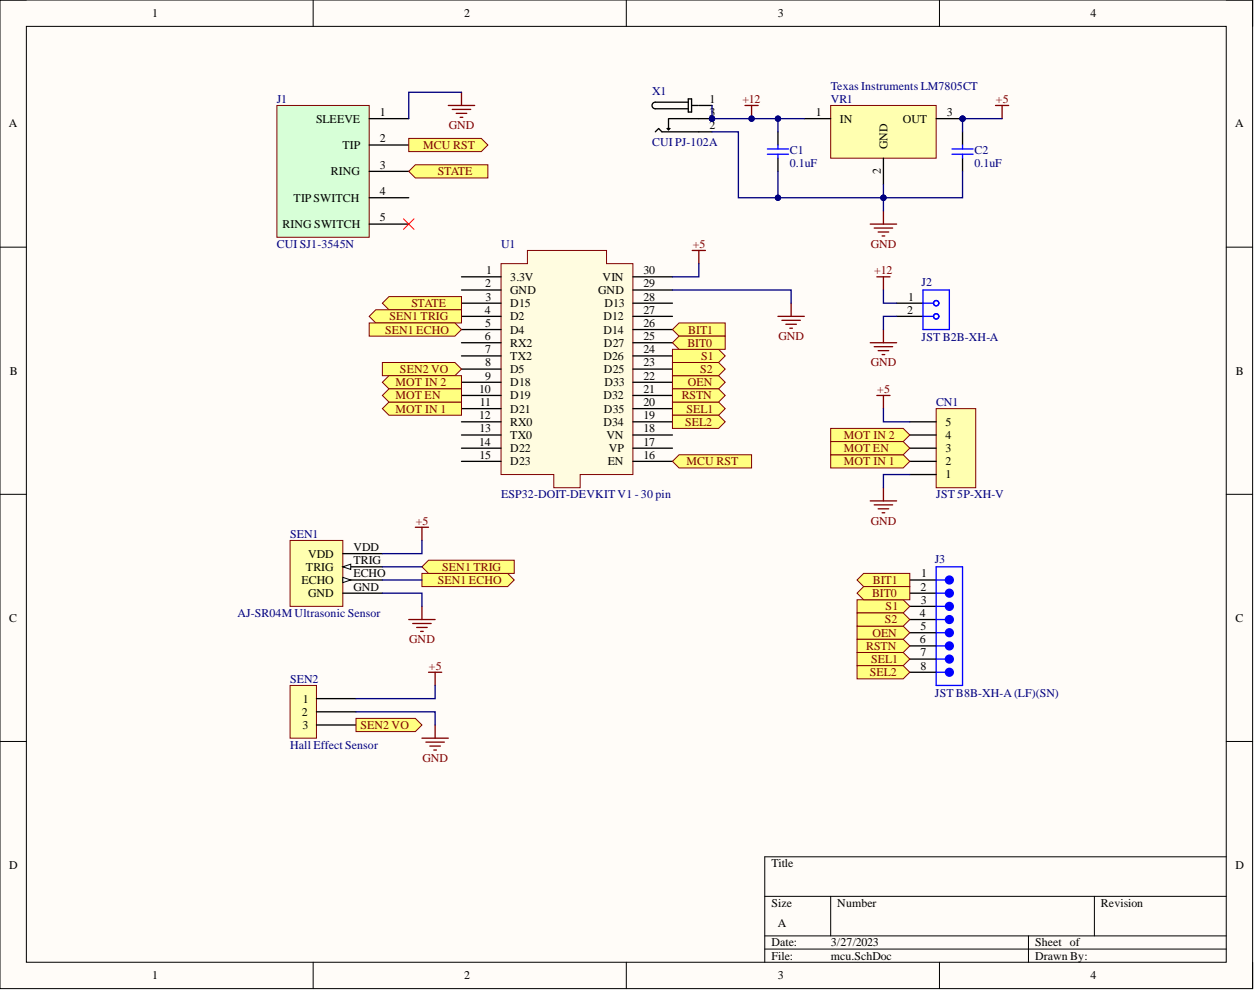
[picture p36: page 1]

JST B8B-XH-A (LF)(SN)

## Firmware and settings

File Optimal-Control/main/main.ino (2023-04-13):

/* IMPORTED LIBRARIES */
#include <HCSR04.h>

/* MISC CONSTANTS */
#define MOTORFREQ 30000
#define LEDFREQ 1
#define PRESETPOINT 1600

/* PINS */
#define MOTORPIN 19
#define IN1PIN 21
#define IN2PIN 18
#define IN1CHANNEL 6
#define IN2CHANNEL 9
#define LEDPIN 23
#define LEDCHANNEL 0
#define SENSOR2PIN 5
#define ECHOPIN 4
#define TRIGGERPIN 2
//#define HOMING 22
/* LED DUTY CYCLES */
#define TENPERC 6554
#define FORTYPERC 26214
#define ONEHUNPERC 65536
#define SEVENTYPERC 45876

/* CONTROL SIGNALS */
#define RSTN 26
#define OEN 25
#define SEL1 27
#define SEL2 14
#define S1  32
#define S2  33

/* COUNTER SIGNALS */
#define BIT0 35
#define BIT1 34 

volatile long count = 0;

/*
  The algorithm below is based on the Example Routine given in the IC datasheet
*/

/* GLOBAL VARIABLE DECLARATION */
volatile double setPosition;
#define KP 0.22
#define KI 0.0
#define KD 0.0
volatile int pulse = 0;
volatile bool home = true;
volatile int state = 1;
bool reset = true;

//volatile double setpoint = 0; // desired
volatile double input = 0;
double error = 0;
double prev_error = 0;
double integral = 0;
double derivative = 0;
unsigned long prev_time = 0;
unsigned long current_time = 0;
int sensor1;
double speed = 0;
double dt;

/* INITIALIZE PID TIMER, MOTOR PID MODEL, AND SENSOR */
hw_timer_t *pidTimer = NULL;
UltraSonicDistanceSensor distanceSensor(TRIGGERPIN, ECHOPIN);

void setup()
{
  Serial.begin(9600);

  // Assign Output Pins
  pinMode(RSTN,OUTPUT);
  pinMode(OEN,OUTPUT);
  pinMode(SEL1,OUTPUT);
  pinMode(SEL2,OUTPUT);
  pinMode(S1,OUTPUT);
  pinMode(S2,OUTPUT);
  pinMode(MOTORPIN, OUTPUT);
  pinMode(IN1PIN, OUTPUT);
  pinMode(IN2PIN, OUTPUT);

  // Assign Input Pins
  pinMode(BIT0,INPUT);
  pinMode(BIT1,INPUT);
  pinMode(SENSOR2PIN, INPUT);
  //pinMode(RESETPIN, INPUT);

  // LED states at 1Hz PWM and 16 bit resolution at channel 0
  ledcAttachPin(LEDPIN, LEDCHANNEL);
  ledcSetup(LEDCHANNEL, LEDFREQ, 16);

  // Motor PWM setup 30kHz at channel 1 and 2 at 8 bit resolution
  ledcAttachPin(IN1PIN, IN1CHANNEL);
  ledcSetup(IN1CHANNEL, MOTORFREQ, 8);
  ledcAttachPin(IN2PIN, IN2CHANNEL);
  ledcSetup(IN2CHANNEL, MOTORFREQ, 8);

  // Initial Decoder Reset
  digitalWrite(RSTN,LOW);
  delay(15);
  digitalWrite(RSTN,HIGH);

  // Initial Control Signals
  digitalWrite(OEN,LOW);
  digitalWrite(SEL1,LOW);
  digitalWrite(SEL2,LOW);
  digitalWrite(S1,LOW);
  digitalWrite(S2,LOW);


  // ISRs
  pidTimer = timerBegin(2, 1, true); // pidTimer number 2, divider = 1 bc no prescalar needed
  timerAttachInterrupt(pidTimer, &PIDFunc, true);
  timerAlarmWrite(pidTimer, 80000, true); // Every 1Khz PID will run 80MHz/80000 = 1Khz

  attachInterrupt(digitalPinToInterrupt(SENSOR2PIN), openClawISR, RISING);
}

void loop()
{
  float distance;
//  if (reset) {
//    while(digitalRead(HOMING) == LOW){
//      ledcWrite(IN1CHANNEL, 255);
//      ledcWrite(IN2CHANNEL, 0);
//    }
//    count = 0;
//    reset = false;
//  }

  switch(state) {
    case 1:
      ledcWrite(LEDCHANNEL, SEVENTYPERC);
   
      distance = distanceSensor.measureDistanceCm();
    
      Serial.print("Distance from object: ");
      Serial.println(distance);
      
      if (distance <= 15 && distance >= 0) {
        digitalWrite(MOTORPIN, HIGH);
        closeClaw();
      }
      break;
    case 2:
      travelClaw();
      break;
    case 3:
      openClaw();
      break;
    case 4:
      // read encoder pulse 
      digitalWrite(OEN, HIGH); // Disable OE
      getPulseCount();
  
      Serial.println("Current pulse: ");+
      Serial.println(count);
      Serial.println("Set position, output: ");
      Serial.println(setPosition);
      Serial.println(speed);      
      break;
    default:
      Serial.println("Error, no such state");
  }
}

void closeClaw()
{
  Serial.println("Entering closeClaw state");
  ledcWrite(LEDCHANNEL, TENPERC);
  setPosition = 2000;

  // Start PID
  home = false;
  state = 4;
  timerAlarmEnable(pidTimer);
}

void PIDFunc()
{
  if (!home)
  {
    int pin;
    int pin2;

    // Motor running to close (forward)
    if (setPosition < count) {
      pin = IN2CHANNEL;
      pin2 = IN1CHANNEL;
    } else {
      // Motor running to open (backward)
      pin = IN1CHANNEL;
      pin2 = IN2CHANNEL;
    }
      pulse = count;
    pid_controller(setPosition, count);
    // slow down motor
    ledcWrite(pin, speed/1.417);
    ledcWrite(pin2, 0);

    // PID settles close enough
    if (speed/1.417 < 3)
    { 
      if (setPosition == 0)
      {
        state = 1;
      }
      else
      {
        state = 2;
      }
      home = true;
    }
  }
}

// PID controller
void pid_controller(double setpoint, double input)
{
    // time difference

    current_time = millis();
    dt = (current_time - prev_time);
    prev_time = current_time;

    dt = dt / 1000.0;

    // error
    error = abs(setpoint - input); // abs(error)?

    // Calculate integral and derivative
    integral += error * dt;
    derivative = (error - prev_error) / dt;

    // Calculate output
    speed = KP * error + KI * integral + KD * derivative;

    // cap pwm to 255
    if (speed > 255)
    {
        speed = 255;
    }

    // Update variables for next iteration
    prev_error = error;
}

void travelClaw()
{
  Serial.println("Entering travelClaw state");
  home = true;
  ledcWrite(LEDCHANNEL, FORTYPERC);

  // Motor stop spin, sanity check
  ledcWrite(IN1CHANNEL, 0);
  ledcWrite(IN2CHANNEL, 0);

  state = 4;
}

void openClawISR() {
  state = 3;
}

// Last state (ISR):
void openClaw()
{
  Serial.println("Entering openClaw state");
  // ISR sense
  ledcWrite(LEDCHANNEL, ONEHUNPERC);
  setPosition = 0;

  // Start PID
  home = false;
  state = 4;
}

/* PLD encoder code*/
byte getByte()
{
byte capture1 = 0; // Initialize a byte variable to read the first capture
for(int i=0; i<4; i++){

  switch(i){
    case 0:
      digitalWrite(S1,LOW);
      digitalWrite(S2,LOW);
      break;
    case 1:
      digitalWrite(S1,HIGH);
      digitalWrite(S2,LOW);
      break;
    case 2:
      digitalWrite(S1,LOW);
      digitalWrite(S2,HIGH);
      break;
    case 3:
      digitalWrite(S1,HIGH);
      digitalWrite(S2,HIGH);
      break; 
    default:
      digitalWrite(S1,LOW);
      digitalWrite(S2,LOW);
      break;
  }

  capture1 |= (digitalRead(BIT0)<<i);
  capture1 |= (digitalRead(BIT1)<<(i+4));
}

byte capture2 = 0; // Initialize a byte variable to read the second capture
for(int i=0; i<4; i++){

  switch(i){
    case 0:
      digitalWrite(S1,LOW);
      digitalWrite(S2,LOW);
      break;
    case 1:
      digitalWrite(S1,HIGH);
      digitalWrite(S2,LOW);
      break;
    case 2:
      digitalWrite(S1,LOW);
      digitalWrite(S2,HIGH);
      break;
    case 3:
      digitalWrite(S1,HIGH);
      digitalWrite(S2,HIGH);
      break; 
    default:
      digitalWrite(S1,LOW);
      digitalWrite(S2,LOW);
      break;
  }

  capture2 |= (digitalRead(BIT0)<<i);
  capture2 |= (digitalRead(BIT1)<<(i+4));
}

if (capture2 == capture1){  // If the first and second capture match then return the result
  byte byteCapture = capture2;
  return byteCapture;  
}
else getByte(); // If the first and second capture DO NOT match, try again to capture 
}

long combine4Bytes(byte byte4, byte byte3, byte byte2, byte byte1)
{
  long combine = 0;
  combine |= (((long)byte4 << 24) | ((long)byte3 << 16) | ((long)byte2 << 8) | ((long)byte1 << 0));
  return combine;
}

void getPulseCount()
{
  delay(25);
  digitalWrite(OEN, HIGH); // Disable OE
  digitalWrite(OEN, LOW); // Enable OE

  // SEL1 = 0 and SEL2 = 1 gets 4th Byte
  digitalWrite(SEL1, LOW);
  digitalWrite(SEL2, HIGH); 
  byte Byte4 = getByte();

  // SEL1 = 1 and SEL2 = 1 gets 3rd Byte
  digitalWrite(SEL1, HIGH);
  digitalWrite(SEL2, HIGH); 
  byte Byte3 = getByte();
  
  // SEL1 = 0 and SEL2 = 0 gets 2nd Byte
  digitalWrite(SEL1, LOW);
  digitalWrite(SEL2, LOW); 
  byte Byte2 = getByte();
  
  // SEL1 = 1 and SEL2 = 0 gets 1st Byte
  digitalWrite(SEL1, HIGH);
  digitalWrite(SEL2, LOW); 
  byte Byte1 = getByte();

  digitalWrite(OEN, HIGH); // disable OE
  delay(25);
  count = combine4Bytes(Byte4,Byte3,Byte2,Byte1);
}

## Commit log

2023-03-05 voltage regulator cct simulated, working
2023-03-10 sw and smlnk files
    [4037N115_Plastic Worm Gear.SLDPRT, 4037N125_Plastic Worm Gear.SLDPRT, 5709K901_Tapered-Roller-Bearing.SLDPRT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]
2023-03-10 8 bit up Counter desig complete, tested
    [PLD Counter Truth Table.xlsx]
2023-03-11 smlnk update
    [Connecting_Rod.SLDPRT, Connecting_Rod_Default_sldprt.STEP, Driven.SLDASM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]
2023-03-14 Base code without PID for control system
2023-03-15 Initial PID controls system
2023-03-15 arduino code for decoder bit translation
2023-03-16 Update LED to work with ESP32
2023-03-16 pid works
    [Connecting_Rod_Default_sldprt.STEP, Fingertip_Grip_sldprt.STEP, Gripper.SLDASM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]
2023-03-16 Update code with ISRs for sensors and PID
2023-03-17 new lead screw pitch
    [Connecting_Rod_Default_sldprt.STEP, Fingertip_Grip_sldprt.STEP, Gripper.SLDASM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]
2023-03-17 Finish base code with PID and encoder pulses parsing
2023-03-18 final model i hope
    [Kinematics.SLDPRT]
2023-03-19 bom for motherboard
    [BOM for motherboard.csv]
2023-03-19 files for the MotorDriver
2023-03-20 PLD code for 4-1 MUX and C++ code for Arduino
2023-03-27 repo cleanup
    [B5B-XH-A.SLDPRT, BOM for MotorDriver.csv, BOM_ for PulseCounter.csv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]
2023-04-11 Add pulse encoder to test and main and fix bugs
    [main.ino, testing.ino]
2023-04-13 PID tuned
2023-04-13 Final without homing
